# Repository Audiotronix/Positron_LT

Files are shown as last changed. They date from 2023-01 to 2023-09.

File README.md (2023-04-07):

<div align="center">

# Positron LT



**Navigation**

| [All Parts (BOM)](/Parts) | [Assembly](/Assembly) | [Software](/Software) | [Gallery](/Gallery) | [Download Repo](../../archive/refs/heads/main.zip)
| --- | --- | --- | --- | --- |

<br>

[](https://discord.gg/HJ44ZeGG2F)

</div>

<br>

## About

The Positron-LT is a printer made for everyone, especially hobbyists and professionals who don't want to or can't use machined parts.
This printer is a [RepRap](https://reprap.org/wiki/RepRap) version based on the innovative [Positron V3](https://github.com/KRALYN/PositronV3) formfactor and motion-system which was created by [KRALYN](https://github.com/KRALYN/PositronV3).

**Although the printer is printed, it can still be folded and thus still fits into a filament box. Thus, there are no disadvantages compared to the original, it may even have some improvements**

> Note: This project is a work in progress! The primary design is ready, updates and changes will be made continuously.

<br>

## LT
**LT** stands for **L**igh**T** 
Since the printer is made of printed parts instead of machined parts, it is lighter than the original Positron V3.

- Lighter to source
- Lighter to build
- Lighter to transport

<br>

## Advantages 

- No Machined Part
-	All mechanical parts can be sourced on websites like AliExpress, Amazon or your local hardware store.
- Much less parts to assemble than the V3
- Integrated PSU (power supply unit) with 200W
- 3mm GT2 timing belt on XY (cheaper and easier to source as the original Synchromesh wire)
- The base chassis is made of 10x10 [Makerbeam](https://www.makerbeam.com/makerbeam/) extrusions and other [Makerbeam](https://www.makerbeam.com/makerbeam/) parts. **All other structural parts can be printed!**
- Simplified Z axis by using a leadscrew. Easy to assemble by folding up
- Improved toolhead cooling
- could be used with larger XY Stepper motors up to 26mm

<br>

## Specs

-	Max Print Speed: 250mm/s (under investigation)
-	Max Travel Speed: 350mm/s (under investigation)
-	Acceleration: 9800mm/s^2 (under investigation)
-	Build Volume: 180x180x180mm
-	Weight: 2300-2500g (with integrated PSU)
-	Hotend max temp: 250C
-	Build Plate Max temp: 80-100C
-	Power supply: 24V; 200W
-	Footprint: ~200mmx200mm

<br>

# RepRap
RepRap means that most parts of the printer can be printed and nothing needs to be machined. Only basic tools like a drill or a saw are needed. All other parts are readily available and can be bought online or might even be available in a hardware store.

<br>

## License

Positron LT is a 3D printer design that is fully open source, which means anyone can use, modify, and share the design. We use a dual-licensing model to ensure that the project remains open source while providing a separate license for entities who want to use the design for financial gain.

### Licensing Explained

- **For personal, educational, and non-commercial use**: The design is available under the GNU General Public License v3.0 (GPLv3). This means you can use, modify, and share the design freely, as long as you also share any changes you make under the same dual-licensing model. This ensures that the open-source nature of the project is maintained. See the [GNU General Public License v3.0 (GPLv3)](LICENSE) file for the full text of the GPLv3.

- **For commercial use or financial gain**: We offer a custom commercial license for companies or individuals who want to use the design for commercial purposes or financial gain. This separate license includes a small royalty fee, which helps support the project. See the [Commercial License](LICENCE-COMMERCIAL) file for details.

### Contributing

We welcome and appreciate contributions to Positron LT! By contributing to this project, you agree that your contributions will be licensed under the dual-licensing model, with the GPLv3 applying to non-commercial use and contributions, and the commercial license applying for commercial use or financial gain.

### License Summary

Positron LT uses a dual-licensing model:

- The GNU General Public License v3.0 (GPLv3) for personal, educational, and non-commercial use and contributions. See the [GNU General Public License v3.0 (GPLv3)](LICENSE) file.
- A commercial license for commercial use or financial gain. See the [Commercial License](LICENCE-COMMERCIAL) file.

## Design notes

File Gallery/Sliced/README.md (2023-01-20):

# This page is still a work in progress! [<sub>(back)</sub>](../../../)
- You will soon find pictures and videos of the printer here

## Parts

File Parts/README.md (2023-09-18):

# The parts that make the Positron LT so great (BOM) [<sub>(back)</sub>](../../../)

| [BOM as .CSV](./bom.csv) | [Required Tools](../Assembly/#required-tools) | [Recommended Filaments](./Printed%20Parts#recommended-filaments) | [Download Printed Parts](https://minhaskamal.github.io/DownGit/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) |
| --- | --- | --- | --- |

>Note: None of these parts need to be machined! Everything can be bought, some parts might need to be shortened with a saw, and some holes need to be drilled, so only basic tools are required.

> There are various display types available. Please make sure you are using the right one

> We currently can not guarantee that all parts fit / work as expected

:exclamation: **These parts are not complete. Printhead and Extruder assemblies may be missing or are currently being developed.** :exclamation:

| You can also install [this extension](https://share-a-cart.com/) and fill your AliExpress cart with just one click.<br>Be aware that this shared cart includes every part besides the makerbeam parts.<br>Things like a raspberry or the psu are also included and might be cheaper when sourced elsewhere.<br><br>Cart id: [I1YPG](https://share-a-cart.com/get/I1YPG)<br><br> We don't know what happens when a store changes it's goods and the shared cart tries to add the product. So please check after importing the cart for completeness.|
| :--- |

</diV>

## [Printed Parts](./Printed%20Parts)

|                   Part Name                   | STL | STEP |Amount| Print Time | Used filament (g)|
| --- | --- | --- | --- | --- | --- |
| BASECOVER_LEFT_V01 | [STL](./Printed%20Parts/STL/BASECOVER_LEFT_V01.stl) | [STEP](./Printed%20Parts/STEP/BASECOVER_LEFT_V01.step) | 1 |  5h27m  |  52  |
| BASECOVER_RIGHT_V01 | [STL](./Printed%20Parts/STL/BASECOVER_RIGHT_V01.stl) | [STEP](./Printed%20Parts/STEP/BASECOVER_RIGHT_V01.step) | 1 |  5h44m  |  54  |
| BASEPART_BACK_V01 | [STL](./Printed%20Parts/STL/BASEPART_BACK_V01.stl) | [STEP](./Printed%20Parts/STEP/BASEPART_BACK_V01.step) | 1 |  6h7m  |  60  |
| BASEPART_FRONT_V01 | [STL](./Printed%20Parts/STL/BASEPART_FRONT_V01.stl) | [STEP](./Printed%20Parts/STEP/BASEPART_FRONT_V01.step) | 1 |  4h38m  |  43  |
| BASEPART_LEFT_V01 | [STL](./Printed%20Parts/STL/BASEPART_LEFT_V01.stl) | [STEP](./Printed%20Parts/STEP/BASEPART_LEFT_V01.step) | 1 |  4h24m  |  38  |
| BASEPART_RIGHT_V01 | [STL](./Printed%20Parts/STL/BASEPART_RIGHT_V01.stl) | [STEP](./Printed%20Parts/STEP/BASEPART_RIGHT_V01.step) | 1 |  4h0m  |  35  |
| BEDHOLDER_CONNECTOR_V01 | [STL](./Printed%20Parts/STL/BEDHOLDER_CONNECTOR_V01.stl) | [STEP](./Printed%20Parts/STEP/BEDHOLDER_CONNECTOR_V01.step) | 1 |  1h33m  |  13  |
| BED_HOLDER_MAIN_V01 | [STL](./Printed%20Parts/STL/BED_HOLDER_MAIN_V01.stl) | [STEP](./Printed%20Parts/STEP/BED_HOLDER_MAIN_V01.step) | 1 |  6h7m  |  60  |
| BELT-TENSIONER_Z_V01 | [STL](./Printed%20Parts/STL/BELT-TENSIONER_Z_V01.stl) | [STEP](./Printed%20Parts/STEP/BELT-TENSIONER_Z_V01.step) | 1 |  15m  |  1  |
| BELT_CONNECTOR_V01_WIP | [STL](./Printed%20Parts/STL/BELT_CONNECTOR_V01_WIP.stl) | [STEP](./Printed%20Parts/STEP/BELT_CONNECTOR_V01_WIP.step) | 1 |  ---  |  ---  |
| BELT_TENSIONER_XY_V01 | [STL](./Printed%20Parts/STL/BELT_TENSIONER_XY_V01.stl) | [STEP](./Printed%20Parts/STEP/BELT_TENSIONER_XY_V01.step) | 1 |  44m  |  6  |
| BOTTOM_COVER_V01 | [STL](./Printed%20Parts/STL/BOTTOM_COVER_V01.stl) | [STEP](./Printed%20Parts/STEP/BOTTOM_COVER_V01.step) | 1 |  19m  |  1  |
| COVER_ROUND_V01 | [STL](./Printed%20Parts/STL/COVER_ROUND_V01.stl) | [STEP](./Printed%20Parts/STEP/COVER_ROUND_V01.step) | 2 |  4m  |  1  |
| DISTANCE_LEFT_V01 | [STL](./Printed%20Parts/STL/DISTANCE_LEFT_V01.stl) | [STEP](./Printed%20Parts/STEP/DISTANCE_LEFT_V01.step) | 1 |  1h44m  |  13  |
| DISTANCE_RIGHT_V01 | [STL](./Printed%20Parts/STL/DISTANCE_RIGHT_V01.stl) | [STEP](./Printed%20Parts/STEP/DISTANCE_RIGHT_V01.step) | 1 |  59m  |  8  |
| ENDCAP_BED-EXTRUSION_V01 | [STL](./Printed%20Parts/STL/ENDCAP_BED-EXTRUSION_V01.stl) | [STEP](./Printed%20Parts/STEP/ENDCAP_BED-EXTRUSION_V01.step) | 2 |  6m  |  1  |
| EXTRUDER_BASEPLATE_V01 | [STL](./Printed%20Parts/STL/EXTRUDER_BASEPLATE_V01.stl) | [STEP](./Printed%20Parts/STEP/EXTRUDER_BASEPLATE_V01.step) | 1 |  7m  |  1  |
| INTERCONNECT_V03_WIP | [STL](./Printed%20Parts/STL/INTERCONNECT_V03_WIP.stl) | [STEP](./Printed%20Parts/STEP/INTERCONNECT_V03_WIP.step) | 1 |  ---  |  ---  |
| LEADSCREW_NUT_MOUNT_V01 | [STL](./Printed%20Parts/STL/LEADSCREW_NUT_MOUNT_V01.stl) | [STEP](./Printed%20Parts/STEP/LEADSCREW_NUT_MOUNT_V01.step) | 1 |  1h2m  |  6  |
| LED_INDICATOR_MOUNT_V01 | [STL](./Printed%20Parts/STL/LED_INDICATOR_MOUNT_V01.stl) | [STEP](./Printed%20Parts/STEP/LED_INDICATOR_MOUNT_V01.step) | 1 |  16m  |  1  |
| MOTORBRACKET_LEFT_V01 | [STL](./Printed%20Parts/STL/MOTORBRACKET_LEFT_V01.stl) | [STEP](./Printed%20Parts/STEP/MOTORBRACKET_LEFT_V01.step) | 1 |  3h17m  |  32  |
| MOTORBRACKET_RIGHT_V01 | [STL](./Printed%20Parts/STL/MOTORBRACKET_RIGHT_V01.stl) | [STEP](./Printed%20Parts/STEP/MOTORBRACKET_RIGHT_V01.step) | 1 |  3h16m  |  32  |
| PICO_MOUNT_PRE-SKETCH_V01 | [STL](./Printed%20Parts/STL/PICO_MOUNT_PRE-SKETCH_V01.stl) | [STEP](./Printed%20Parts/STEP/PICO_MOUNT_PRE-SKETCH_V01.step) | 1 |  20m  |  2  |
| SCREEN_BASE_V01_WIP | [STL](./Printed%20Parts/STL/SCREEN_BASE_V01_WIP.stl) | [STEP](./Printed%20Parts/STEP/SCREEN_BASE_V01_WIP.step) | 1 |  1h57m  |  20  |
| SCREEN_LID_V01_WIP | [STL](./Printed%20Parts/STL/SCREEN_LID_V01_WIP.stl) | [STEP](./Printed%20Parts/STEP/SCREEN_LID_V01_WIP.step) | 1 |  1h6m  |  9  |
| SCREWMOUNT_BOTTOM_V01 | [STL](./Printed%20Parts/STL/SCREWMOUNT_BOTTOM_V01.stl) | [STEP](./Printed%20Parts/STEP/SCREWMOUNT_BOTTOM_V01.step) | 1 |  59m  |  7  |
| SIDE_PANEL_LEFT_V01 | [STL](./Printed%20Parts/STL/SIDE_PANEL_LEFT_V01.stl) | [STEP](./Printed%20Parts/STEP/SIDE_PANEL_LEFT_V01.step) | 1 |  44m  |  5  |
| SIDE_PANEL_RIGHT_V01 | [STL](./Printed%20Parts/STL/SIDE_PANEL_RIGHT_V01.stl) | [STEP](./Printed%20Parts/STEP/SIDE_PANEL_RIGHT_V01.step) | 1 |  44m  |  5  |
| X-RAIL_ENDCAP_V01 | [STL](./Printed%20Parts/STL/X-RAIL_ENDCAP_V01.stl) | [STEP](./Printed%20Parts/STEP/X-RAIL_ENDCAP_V01.step) | 2 |  6m  |  1  |
| XY-SPACER_V01 | [STL](./Printed%20Parts/STL/XY-SPACER_V01.stl) | [STEP](./Printed%20Parts/STEP/XY-SPACER_V01.step) | 1 |  21m  |  3  |
| Z-AXIS-ENDSTOP_V01 | [STL](./Printed%20Parts/STL/Z-AXIS-ENDSTOP_V01.stl) | [STEP](./Printed%20Parts/STEP/Z-AXIS-ENDSTOP_V01.step) | 1 |  1h2m  |  8  |
| Z-BLOCK_HOLDER_V01 | [STL](./Printed%20Parts/STL/Z-BLOCK_HOLDER_V01.stl) | [STEP](./Printed%20Parts/STEP/Z-BLOCK_HOLDER_V01.step) | 1 |  42m  |  5  |

``Click on the links to be redirected to the file``<br>
``Print time and part weight are a result of slicing the parts in PrusaSlicer with .20 layer height (quality) for the PrusaMini``

<br>

## [Mechanical Parts](./Mechanical%20Parts)

### EXTRUDER:
|                    Part Name                    |CAD|                               Link                              |PCS | Price |                                                                                                                                 Note                                                                                                                                 |
| --- | --- | :---: | :---: | :---: | :--- |
| [ANGLED_EXTRUDER_MOD](./Mechanical%20Parts/ANGLED_EXTRUDER_MOD.stl) | 1 | [link](https://github.com/FramingApp/PositronV3B-High-Speed-Edition/blob/10x10makerbeams_w_screw_z_axis/CAD%20%20files/Angled%20Extruder%20Mod.stp) | --- | --- | Designed by HarryLoud: [link](https://github.com/FramingApp/PositronV3B-High-Speed-Edition/blob/10x10makerbeams_w_screw_z_axis/CAD%20%20files/Angled%20Extruder%20Mod.stp) |
| [CAPRICORN_PTFE_TUBE_1](./Mechanical%20Parts/CAPRICORN_PTFE_TUBE_1.stl) | 1 | [link](https://aliexpress.com/item/1005003433217588.html) / [link](https://amzn.to/3jBuaMN) | 1 | 8,25€ | About 60cm required |
| [HOTEND_COMPLETE](./Mechanical%20Parts/HOTEND_COMPLETE.stl) | 1 | [link](https://aliexpress.com/item/1005004802238357.html) | 1 | 35,77€ | Funssor hotend complete / will be replaced with Phaetus hotend when available  |

### ELECTRONICS:
|                    Part Name                    |CAD|                               Link                              |PCS | Price |                                                                                                                                 Note                                                                                                                                 |
| --- | --- | :---: | :---: | :---: | :--- |
| [10PIN_EXP_FEMALE](./Mechanical%20Parts/10PIN_EXP_FEMALE.stl) | 1 | [link](https://aliexpress.com/item/1005002431897617.html) | 10 | 0,88€ | Select 10P |
| [10PIN_MALE_CONNECTOR](./Mechanical%20Parts/10PIN_MALE_CONNECTOR.stl) | 1 | [link](https://aliexpress.com/item/33029492417.html) / [link](https://amzn.to/3XzUQMl) | 1 | 1,12€ | Select 2x5 10pin |
| [6_PIN_MAGNETIC_POGO](./Mechanical%20Parts/6_PIN_MAGNETIC_POGO.stl) | 1 | [link](https://aliexpress.com/item/1005002669709542.html) | 1 | 3,30€ | Select 6pin Straight |
| [C7_PLUG-IN](./Mechanical%20Parts/C7_PLUG-IN.stl) | 1 | [link](https://aliexpress.com/item/4001252791878.html) | 1 | 0,23€ |  |
| [CABLE_C7_SWITCH](./Mechanical%20Parts/CABLE_C7_SWITCH.stl) | 1 | [link](https://amzn.to/3w4nDgk) / [link](https://amzn.to/3XzU6qx) | 1 | 9,99€ | We recommend using a cable with a switch or an adapter like this: [link](https://aliexpress.com/item/1005002301827800.html) / [link](https://amzn.to/3XzSGfH) |
| [EPP-200-24](./Mechanical%20Parts/EPP-200-24.stl) | 1 | [link](https://www.mouser.de/ProductDetail/MEAN-WELL/EPP-200-24?qs=C9r8PV%2F%252BoWOh4U0pNOxnkQ%3D%3D) / [link](https://amzn.to/3WfsBS9) | 1 | 52,30€ | Meanwell EPP-200-24 !! Note from Muon3D: If theMuon3D heated bed is being used, the EPP-200-27 improves its performance by 30-40%. (70-80w at 24v, 90-100w at 27v). [link](https://www.mouser.de/ProductDetail/MEAN-WELL/EPP-200-27?qs=C9r8PV%2F%252BoWPXQf6mJFm6HA%3D%3D) |
| [FAN_2510](./Mechanical%20Parts/FAN_2510.stl) | 2 | [link](https://aliexpress.com/item/32807610078.html) / [link](https://amzn.to/3iCEaVR) | 2 | 10,69€ | 24V Dual Ball XH2,54 |
| [FAN_3010](./Mechanical%20Parts/FAN_3010.stl) | 1 | [link](https://aliexpress.com/item/1005002568592831.html?) | 1 | 3,59€ | Select 24V xh2.54 2pin |
| [FAN_5015](./Mechanical%20Parts/FAN_5015.stl) | 1 | [link](https://aliexpress.com/item/1005002517858129.html) / [link](https://aliexpress.com/item/32844339310.html) | 1 | 8,67€ | Select 24V model |
| [HEATED_GLASSBED_MUON-3D](./Mechanical%20Parts/HEATED_GLASSBED_MUON-3D.stl) | 1 | [link](https://muon3d.com/products/positron-v3-transparent-heated-bed) | 1 | 45,95€ | Highly recomended !! Note from Muon3D: If theMuon3D heated bed is being used, the EPP-200-27 improves its performance by 30-40%. (70-80w at 24v, 90-100w at 27v). [link](https://www.mouser.de/ProductDetail/MEAN-WELL/EPP-200-27?qs=C9r8PV%2F%252BoWPXQf6mJFm6HA%3D%3D) |
| [HEATER_CARTRIGE_1](./Mechanical%20Parts/HEATER_CARTRIGE_1.stl) | 1 | [link](https://aliexpress.com/item/32843289523.html) | 1 | 1,27€ | Select 24V 50W 1M |
| [HEAT_SINK_RPI_2MM](./Mechanical%20Parts/HEAT_SINK_RPI_2MM.stl) | 1 | [link](https://aliexpress.com/item/1005004772727034.html) | 1 | 5,72€ | 2mm height |
| [LED_4X_15X15](./Mechanical%20Parts/LED_4X_15X15.stl) | 1 | [link](https://aliexpress.com/item/1005002674028098.html) | 1 | 0,45€ | Select 4Bit Rectangular |
| [MINI_IR_SENSOR](./Mechanical%20Parts/MINI_IR_SENSOR.stl) | 1 | [link](https://aliexpress.com/item/32995184975.html) | 1 | 18,20€ |  |
| [MOTOR_17HS08-1004S](./Mechanical%20Parts/MOTOR_17HS08-1004S.stl) | 3 | [link](https://www.omc-stepperonline.com/de/nema-17-bipolar-0-9deg-11ncm-15-6oz-in-1-2a-3-6v-42x42x21mm-4-draehte-17hm08-1204s) / [link](https://amzn.to/3iEKg85) | 1 | 8,28€ |  |
| [RPI_ZERO_2W](./Mechanical%20Parts/RPI_ZERO_2W.stl) | 1 | [link](https://www.reichelt.de/raspberry-pi-zero-2-w-4x-1-ghz-512-mb-ram-wlan-bt-rasp-pi-zero2-w-p313902.html) / [link](https://amzn.to/3IR9ASM) | 1 | 22,50€ | You can also use an Bananapi Pi M2 Zero as substituion: [link](https://github.com/FramingApp/BananaPi_Positron_Klipper_Moonraker_Fluidd) |
| [SKR-PICO](./Mechanical%20Parts/SKR-PICO.stl) | 1 | [link](https://biqu.equipment/en-au/products/btt-skr-pico-v1-0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) / [link](https://amzn.to/3QKw7Tj) | 1 | 29,99€ |  |
| [TFT_35](./Mechanical%20Parts/TFT_35.stl) | 1 | [link](https://aliexpress.com/item/1005004864671870.html) / [link](https://amzn.to/3l8vAPt) | 1 | 17,34€ |  |
| [THERMISTOR_1](./Mechanical%20Parts/THERMISTOR_1.stl) | 1 | [link](aliexpress.com/item/32812361274.html) / [link](https://amzn.to/3Y2qRxg) | 5 | 2,17€ | Select with XH2.54 terminal |

### FASTENERS:
|                    Part Name                    |CAD|                               Link                              |PCS | Price |                                                                                                                                 Note                                                                                                                                 |
| --- | --- | :---: | :---: | :---: | :--- |
| [DIN_7979_M3X4X12](./Mechanical%20Parts/DIN_7979_M3X4X12.stl) | 2 | [link](https://aliexpress.com/item/1005003200850626.html) | 5 | 4,30€ | Select M3 (OD 4mm), 12mm (5pcs) |
| [DIN_7991_M3X12](./Mechanical%20Parts/DIN_7991_M3X12.stl) | 4 | [link](https://aliexpress.com/item/1005003107985358.html) / [link](https://amzn.to/3lbRscQ) | 50 | 2,06€ |  |
| [DIN_7991_M3X14](./Mechanical%20Parts/DIN_7991_M3X14.stl) | 41 | [link](https://aliexpress.com/item/1005003107985358.html) / [link](https://amzn.to/3JEOpDX) | 50 | 2,28€ |  |
| [DIN_7991_M3X16](./Mechanical%20Parts/DIN_7991_M3X16.stl) | 4 | [link](https://aliexpress.com/item/1005003107985358.html) / [link](https://amzn.to/3l1bwhH) | 50 | 2,04 |  |
| [DIN_7991_M3X18](./Mechanical%20Parts/DIN_7991_M3X18.stl) | 7 | [link](https://aliexpress.com/item/1005003107985358.html) | 50 | 2,99€ |  |
| [DIN_7991_M3X25](./Mechanical%20Parts/DIN_7991_M3X25.stl) | 5 | [link](https://aliexpress.com/item/1005003107985358.html) / [link](https://amzn.to/3WZ3N0Z) | 50 | 3,68€ |  |
| [DIN_7991_M3X35](./Mechanical%20Parts/DIN_7991_M3X35.stl) | 12 | [link](https://aliexpress.com/item/1005003107985358.html) | 50 | 4,72€ |  |
| [DIN_7991_M3X8](./Mechanical%20Parts/DIN_7991_M3X8.stl) | 8 | [link](https://aliexpress.com/item/1005003107985358.html) / [link](https://amzn.to/3wUBpmc) | 50 | 1,58€ |  |
| [DIN_912_M3X20](./Mechanical%20Parts/DIN_912_M3X20.stl) | 5 | [link](https://aliexpress.com/item/1005003106092326.html) | 10 | 1,48€ |  |
| [DIN_912_M3X6](./Mechanical%20Parts/DIN_912_M3X6.stl) | 10 | [link](https://aliexpress.com/item/1005003106092326.html) | 10 | 0,78€ |  |
| [DIN_934_M3](./Mechanical%20Parts/DIN_934_M3.stl) | 2 | [link](https://aliexpress.com/item/1005003106199633.html) | 50 | 1,36€ |  |
| [M3_INSERT](./Mechanical%20Parts/M3_INSERT.stl) | 22 | [link](https://aliexpress.com/item/1005004879644825.html) / [link](https://amzn.to/3CRKrUf) | 50 | 0,35€ | Select M3(OD4.5mm), Length 5mm 50pcs |
| [THUMBSCREW_M6X16](./Mechanical%20Parts/THUMBSCREW_M6X16.stl) | 1 | [link](https://aliexpress.com/item/1005004651298319.html) | 2 | 1,90€ | Select M6 2pcs, 16mm |
| [WAFERHEAD_M3X10](./Mechanical%20Parts/WAFERHEAD_M3X10.stl) | 19 | [link](https://aliexpress.com/item/1005004510664424.html) | 20 | 1,97€ |  |
| [WAFERHEAD_M3X14](./Mechanical%20Parts/WAFERHEAD_M3X14.stl) | 4 | [link](https://aliexpress.com/item/1005004510664424.html) | 20 | 2,10€ |  |
| [WAFERHEAD_M3X20](./Mechanical%20Parts/WAFERHEAD_M3X20.stl) | 5 | [link](https://aliexpress.com/item/1005004510664424.html) | 20 | 2,54€ |  |

### MAKERBEAM:
Since Makerbeam does not sell beams with the needed length, they can either be cut by makerbeam or yourself. A cut by makerbeam costs 3.50€ you can find that service here:  [link](https://www.makerbeam.com/cut-and-tap-for-10x10mm.html) . Either way, you need to buy beams that are able to be cut in the desired lengths for which we created a cutting plan that can be found here: [link](https://github.com/Audiotronix/Positron_LT/blob/main/Parts/makerbeam_cuttingplan.pdf)
|                    Part Name                    |CAD|                               Link                              |PCS | Price |                                                                                                                                 Note                                                                                                                                 |
| --- | --- | :---: | :---: | :---: | :--- |
| [DIN_34805_M3X4](./Mechanical%20Parts/DIN_34805_M3X4.stl) | 7 |  | 25 | --- | Included with T-slot nut |
| [DIN_7991_M3X4](./Mechanical%20Parts/DIN_7991_M3X4.stl) | 3 |  | 25 | --- | Included with T-slot nut |
| [MAKERBEAM-CUBE](./Mechanical%20Parts/MAKERBEAM-CUBE.stl) | 3 | [link](https://www.makerbeam.com/makerbeam-corner-cubes-12p-black-for-makerbeam.html?id=24117589) / [link](https://amzn.eu/2M0ya10) | 12 | 17,95€ | You can buy single cubes here: [link](https://amzn.eu/2M0ya10) |
| [MAKERBEAM-CUBE_M6](./Mechanical%20Parts/MAKERBEAM-CUBE_M6.stl) | 1 |  | --- | --- | Included in previous cube order if ordered from makerbeam, otherwise can be ordered here: [link](https://amzn.eu/2M0ya10) |
| [MAKERBEAM_L-BRACKET_100304](./Mechanical%20Parts/MAKERBEAM_L-BRACKET_100304.stl) | 7 | [link](https://www.makerbeam.com/makerbeam-90-degree-brackets-12p.html?id=24117637) | 12 | 6,95€ |  |
| [MAKERBEAM_L165](./Mechanical%20Parts/MAKERBEAM_L165.stl) | 2 | [link](https://www.makerbeam.com/makerbeam/makerbeam-10x10mm-profile-lengths-anodised-in-blac/) | --- | -> | You can find more infos about the beams in the text below the category name [link](https://github.com/Audiotronix/Positron_LT/tree/main/Parts#makerbeam) |
| [MAKERBEAM_L200](./Mechanical%20Parts/MAKERBEAM_L200.stl) | 2 | [link](https://www.makerbeam.com/makerbeam/makerbeam-10x10mm-profile-lengths-anodised-in-blac/) | --- | -> | You can find more infos about the beams in the text below the category name [link](https://github.com/Audiotronix/Positron_LT/tree/main/Parts#makerbeam) |
| [MAKERBEAM_L230](./Mechanical%20Parts/MAKERBEAM_L230.stl) | 1 | [link](https://www.makerbeam.com/makerbeam/makerbeam-10x10mm-profile-lengths-anodised-in-blac/) | --- | -> | You can find more infos about the beams in the text below the category name [link](https://github.com/Audiotronix/Positron_LT/tree/main/Parts#makerbeam) |
| [MAKERBEAM_L240](./Mechanical%20Parts/MAKERBEAM_L240.stl) | 2 | [link](https://www.makerbeam.com/makerbeam/makerbeam-10x10mm-profile-lengths-anodised-in-blac/) | --- | -> | You can find more infos about the beams in the text below the category name [link](https://github.com/Audiotronix/Positron_LT/tree/main/Parts#makerbeam) |
| [MAKERBEAM_L250](./Mechanical%20Parts/MAKERBEAM_L250.stl) | 3 | [link](https://www.makerbeam.com/makerbeam/makerbeam-10x10mm-profile-lengths-anodised-in-blac/) | --- | -> | You can find more infos about the beams in the text below the category name [link](https://github.com/Audiotronix/Positron_LT/tree/main/Parts#makerbeam) |
| [MAKERBEAM_L30](./Mechanical%20Parts/MAKERBEAM_L30.stl) | 1 | [link](https://www.makerbeam.com/makerbeam/makerbeam-10x10mm-profile-lengths-anodised-in-blac/) | --- | -> | You can find more infos about the beams in the text below the category name [link](https://github.com/Audiotronix/Positron_LT/tree/main/Parts#makerbeam) |
| [MAKERBEAM_T-NUT_101619-1](./Mechanical%20Parts/MAKERBEAM_T-NUT_101619-1.stl) | 33 | [link](https://www.makerbeam.com/makerbeam-t-slot-nuts-for-makerbeam-25p.html) / [link](https://amzn.to/3DGxXPI) | 25 | 14,98€ | Order the big pack: [link](https://www.makerbeam.com/makerbeam-t-slot-nuts-for-makerbeam-25p.html) and a small one: [link](https://www.makerbeam.com/linear-slide-kit-t-slot-nuts-5p-and-5mm-bolts-m3-1.html) / [link](https://amzn.to/3DGxXPI) |

### MOTION:
|                    Part Name                    |CAD|                               Link                              |PCS | Price |                                                                                                                                 Note                                                                                                                                 |
| --- | --- | :---: | :---: | :---: | :--- |
| [F5-10_BEARING](./Mechanical%20Parts/F5-10_BEARING.stl) | 2 | [link](https://aliexpress.com/item/4000211452548.html) / [link](https://amzn.to/3l24CZH) | 1 | 0,27€ |  |
| [F683_OPEN_BEARING-H25-](./Mechanical%20Parts/F683_OPEN_BEARING-H25-.stl) | 28 | [link](aliexpress.com/item/1005004282333265.html) | 10 | 2,95€ | Select 3 times |
| [GT2_16T_IDLER_SMOOTH](./Mechanical%20Parts/GT2_16T_IDLER_SMOOTH.stl) | 1 | [link](https://aliexpress.com/item/32971394035.html) / [link](https://amzn.to/3DF3bad) | 1 | 0,55€ | Select 16T W6 B3 Without T |
| [GT2_BELT-3MM_L1650MM](./Mechanical%20Parts/GT2_BELT-3MM_L1650MM.stl) | 1 | [link](https://www.ebay.de/itm/283457733982?var=585183190920) / [link](https://amzn.to/3wUc9MT) | 1 | 5,00€ | Select x 2m (Y32) (You also can cut an 6mm belt in 2pieces. recommented cut at~2,8mm) |
| [GT2_BELT-6MM_L178MM](./Mechanical%20Parts/GT2_BELT-6MM_L178MM.stl) | 1 | [link](https://aliexpress.com/item/1005004100120790.html) / [link](https://amzn.to/3DIaihV) | 1 | 1,07€ | Select 2GT-178, Belt Width 6mm 1pcs |
| [LEADSCREW_NUT_T5X4](./Mechanical%20Parts/LEADSCREW_NUT_T5X4.stl) | 1 | [link](https://www.ebay.de/itm/165688561910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) | 1 | 1,49€ | Only needs to be bought if no screw is included with rod! Select T5x1x4 Brass/POM |
| [LEADSCREW_T5X4_L225](./Mechanical%20Parts/LEADSCREW_T5X4_L225.stl) | 1 | [link](https://aliexpress.com/item/1005004583759873.html) / [link](https://www.ebay.de/itm/165688561901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) | 1 | 10,15€ | Select 250mm, Pitch 1mm Lead 4mm / Second link has no screw! |
| [MF85_BEARING](./Mechanical%20Parts/MF85_BEARING.stl) | 2 | [link](https://aliexpress.com/item/1005004881583203.html) / [link](https://amzn.to/3HTb6mI) | 1 | 0,72€ | Select MF85ZZ 5X8X2.5mm |
| [MGN12-C_CARRIAGE](./Mechanical%20Parts/MGN12-C_CARRIAGE.stl) | 1 |  | 1 | --- | Mostly includet with the rails |
| [MGN12_RAIL_L225](./Mechanical%20Parts/MGN12_RAIL_L225.stl) | 1 | [link](https://amzn.to/3H8WS0A) | 1 | 18,99€ | 250mm MGN12C |
| [MGN9-C_CARRIAGE](./Mechanical%20Parts/MGN9-C_CARRIAGE.stl) | 1 |  | 1 | --- | Mostly includet with the rails |
| [MGN9_RAIL_L227](./Mechanical%20Parts/MGN9_RAIL_L227.stl) | 1 | [link](https://amzn.to/3Wfy7UH) | 1 | 20,99€ | 250mm MGN9C |
| [MGW9-C_CARRIAGE](./Mechanical%20Parts/MGW9-C_CARRIAGE.stl) | 1 |  | 1 | --- | Mostly includet with the rails |
| [MGW9_RAIL_L227](./Mechanical%20Parts/MGW9_RAIL_L227.stl) | 1 | [link](https://www.ebay.de/itm/234306987115?var=533899872753) / [link](https://amzn.to/3Xxt5Uz) | 1 | 19,40€ | 250mm MGW9C |
| [MR115_BEARING](./Mechanical%20Parts/MR115_BEARING.stl) | 1 | [link](https://aliexpress.com/item/32995122493.html) / [link](https://amzn.to/3HvHSsA) | 10 | 0,94€ |  |
| [MR117_2Z_BEARING](./Mechanical%20Parts/MR117_2Z_BEARING.stl) | 10 | [link](https://aliexpress.com/item/4000891798197.html) / [link](https://amzn.to/3RulK6u) | 5 | 2,71€ | Select MR117ZZ 7x11x3mm |
| [PULLEY_T20_LOWPROFILE](./Mechanical%20Parts/PULLEY_T20_LOWPROFILE.stl) | 4 | [link](https://aliexpress.com/item/32913757229.html) | 1 | 0,99€ | Select 20T Bore 5mm |

### SHIMS:
|                    Part Name                    |CAD|                               Link                              |PCS | Price |                                                                                                                                 Note                                                                                                                                 |
| --- | --- | :---: | :---: | :---: | :--- |
| [DIN_125_M5](./Mechanical%20Parts/DIN_125_M5.stl) | 2 | [link](https://aliexpress.com/item/1005002148389665.html) | 25 | 1,48€ | Select M5(25PCS) |
| [DIN_433_M3](./Mechanical%20Parts/DIN_433_M3.stl) | 12 | [link](https://aliexpress.com/item/4001213983709.html) | 100 | 2,21€ | Select 3x6x0.5 |
| [DIN_988_7X13X02](./Mechanical%20Parts/DIN_988_7X13X02.stl) | 40 | [link](https://aliexpress.com/item/1005002046188859.html) / [link](https://amzn.to/3DF8rdF) | 50 | 1,91€ | Select 50pcs M7x13xThick, Thick 0.2mm |
| [DIN_988_M3X02](./Mechanical%20Parts/DIN_988_M3X02.stl) | 8 | [link](https://aliexpress.com/item/1005001878233881.html) / [link](https://amzn.to/3X3Y1LN) | 50 | 1,26€ | Select M3x6xThick 50pcs, 0.2mm thick |

|                    Part Name                    |CAD|                               Link                              |PCS | Price |                                                                                                                                 Note                                                                                                                                 |
| --- | --- | :---: | :---: | :---: | :--- |
| [BUFFER_BOTTOM](./Mechanical%20Parts/BUFFER_BOTTOM.stl) | 4 | [link](https://aliexpress.com/item/1005001559607723.html) | 100 | 1,06€ |  |
| [DUST_COVER_85X52](./Mechanical%20Parts/DUST_COVER_85X52.stl) | 2 | [link](https://aliexpress.com/item/4001283014835.html) | --- | --- | Highly recommended!  need to be cutted in 85x52mm and clued under the air shrout left and right |
| [PCB_SCREEN_ADAPTER](./Mechanical%20Parts/PCB_SCREEN_ADAPTER.stl) | 1 |  | --- | --- | Custom PCB, WIP |
| [SILICONE_SOCK_1](./Mechanical%20Parts/SILICONE_SOCK_1.stl) | 1 |  | --- | --- | Needs to be molded by yourself (WIP) |
| [SPACER_PRINTBED_WIP](./Mechanical%20Parts/SPACER_PRINTBED_WIP.stl) | 2 |  | --- | --- | Bed-End-Spacer WIP |

``Click on the part name to see a 3D model of it (mechanical parts are not intedet to be printed!)``<br>
``Price is based on the first/main link of each product``

> Note: Some links might be affiliate links!

## Total
| Category | Total | Exact Price |
| --- | --- | --- |
| EXTRUDER | 44,02€ | 44,02€ |
| ELECTRONICS | 259,2€ | 256,67€ |
| FASTENERS | 36,13€ | 11,67€ |
| MAKERBEAM | 54,86€<br>+29,35€ | 28,31€<br>+29,35€ |
| MOTION | 98,79€ | 97,35€ |
| SHIMS | 6,86€ | 2,12€ |
| OTHER | 1,06€ | 0,04€ |
| | | |
| Total | 530,27€ | 469,53€ |

> Note: Prices were calculated 20.01.2023, so might no longer be accurate

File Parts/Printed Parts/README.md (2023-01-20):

# Printing the Positron LT parts
| [Download 3D Files](https://minhaskamal.github.io/DownGit/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) |
| --- |

>Note: These are suggestions, I designed the LT with these in mind but other settings might work aswell. The Design is based on an 0.4mm Nozzle

## Recommended Filaments:

>Note: We absolutely recommend using a technical material without any flexibility that can withstand high temperatures. Tested Filaments:

| Type | Brand | Name | Price | Link | Required Nozzle |
| --- | --- | --- | --- | --- | --- |
| PC Blend | Prusament | Carbon Fiber | 59.99€ | [link](https://www.prusa3d.com/product/prusament-pc-blend-carbon-fiber-black-800g-2/) | Hardened |
| GreenTEC | extrudr | Pro Carbon | 49.99€ | [link](https://amzn.to/3ZJIYcK) | Hardened |
| ASA | Prusament | Prusament ASA | 29.99€ | [link](https://www.prusa3d.com/category/prusament-asa/) | --- |

> Note: Some links might be affiliate links!

## Slicing:

| Layer height | Infill | Supports | Perimeters | Horizontal shells | 
| --- | --- | --- | --- | --- |
| 0.2mm | 40% | On build plate only | 5 (min) | Top: 9, Bot: 8 |

## Printing:
| Part Name | Orientation | Supports | Prepared |
| :---: | --- | --- | --- |
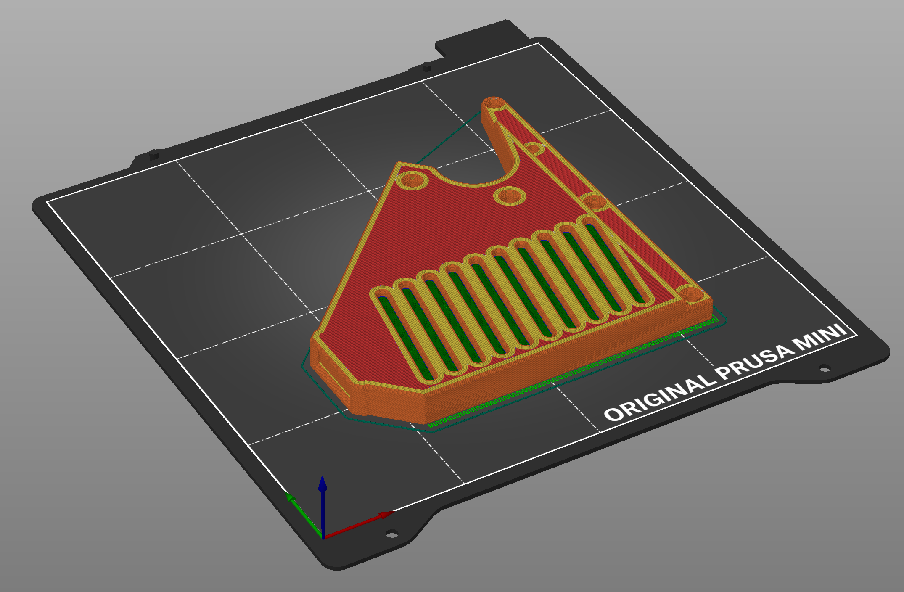
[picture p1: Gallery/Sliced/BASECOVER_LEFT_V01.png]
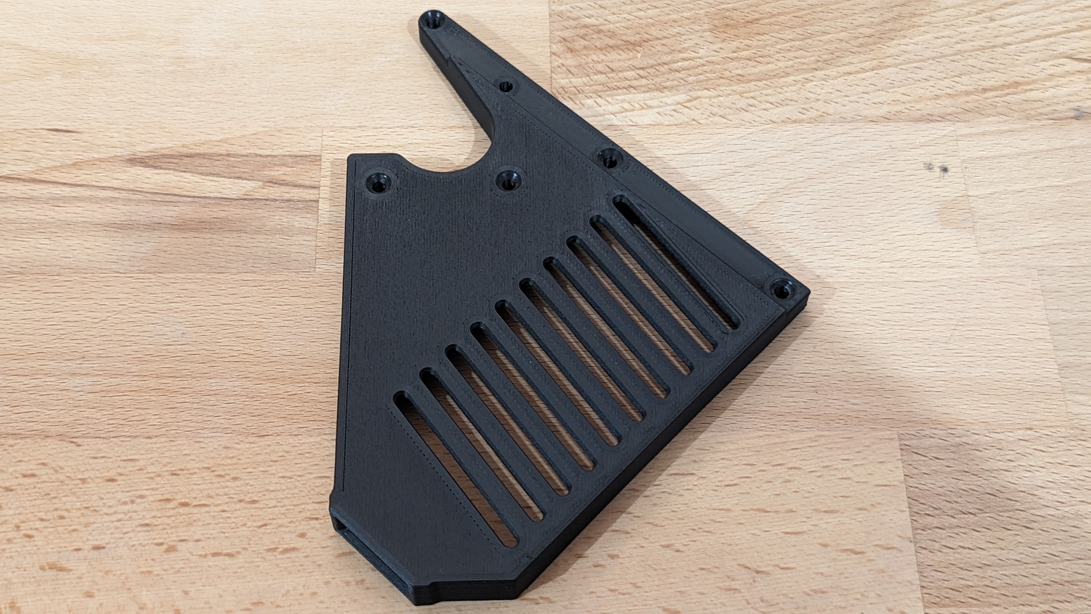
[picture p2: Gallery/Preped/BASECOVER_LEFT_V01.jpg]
|[BASECOVER_LEFT_V01](./STL/BASECOVER_LEFT_V01.stl) |  |  Supports on build plate only  | |
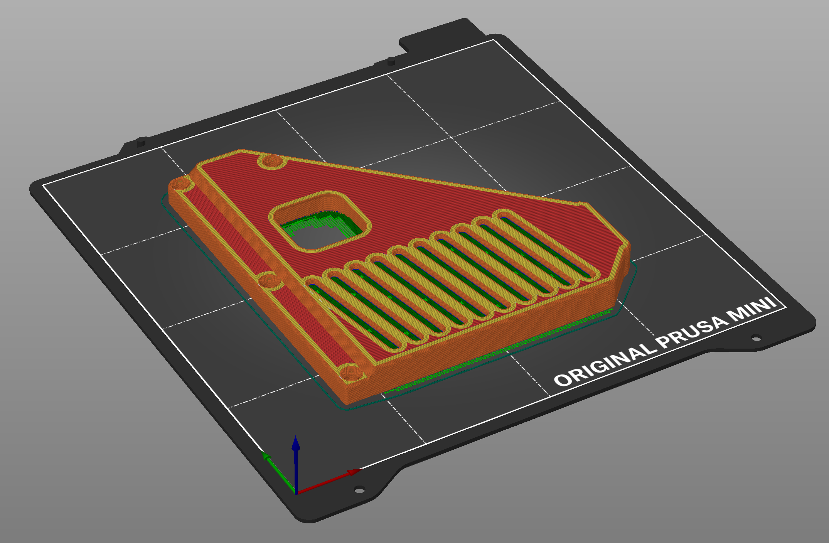
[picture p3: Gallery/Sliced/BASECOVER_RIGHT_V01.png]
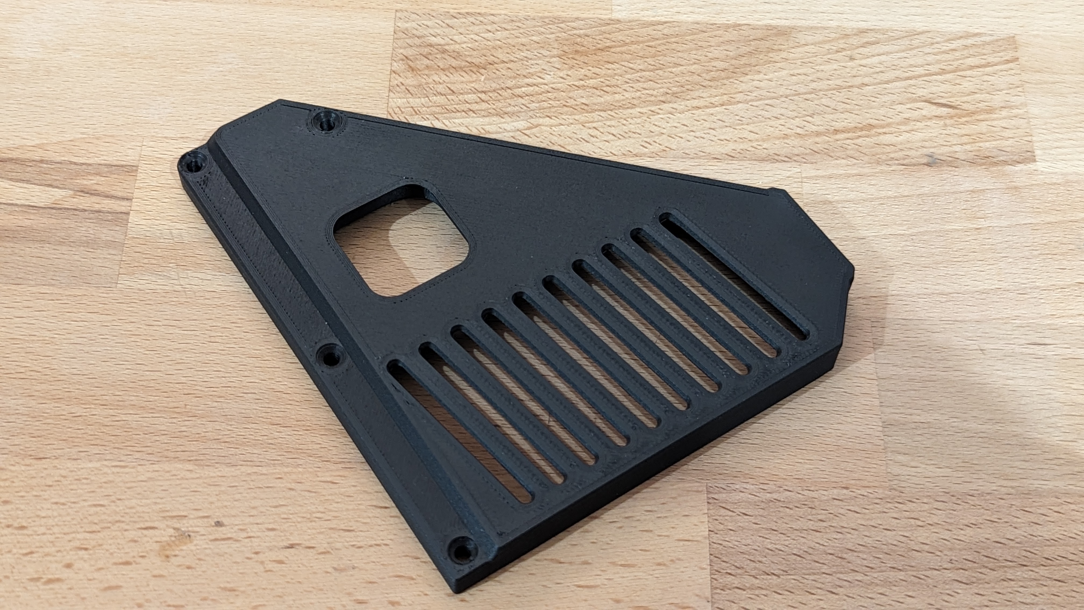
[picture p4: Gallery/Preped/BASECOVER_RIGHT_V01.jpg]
|[BASECOVER_RIGHT_V01](./STL/BASECOVER_RIGHT_V01.stl) |  |  Supports on build plate only  | |
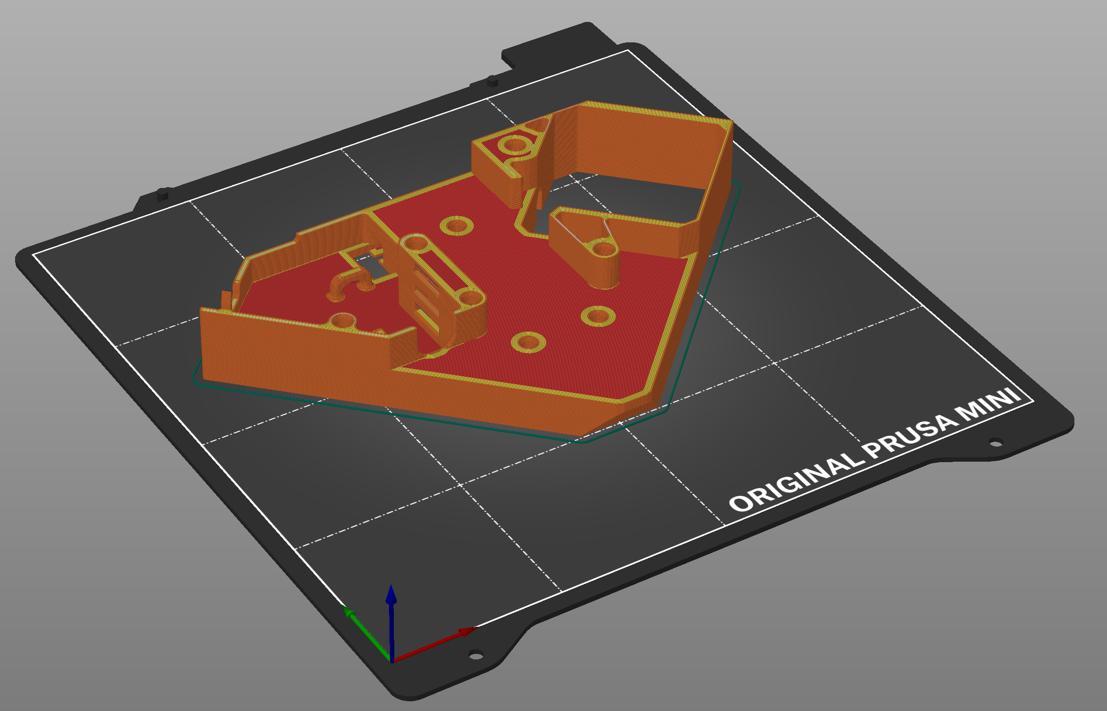
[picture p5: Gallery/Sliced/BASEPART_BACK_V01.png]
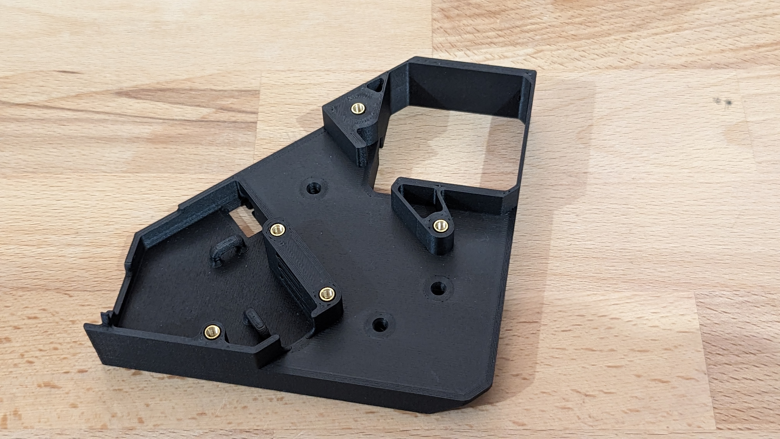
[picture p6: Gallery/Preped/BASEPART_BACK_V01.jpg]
|[BASEPART_BACK_V01](./STL/BASEPART_BACK_V01.stl) |  |  No supports needed  | |
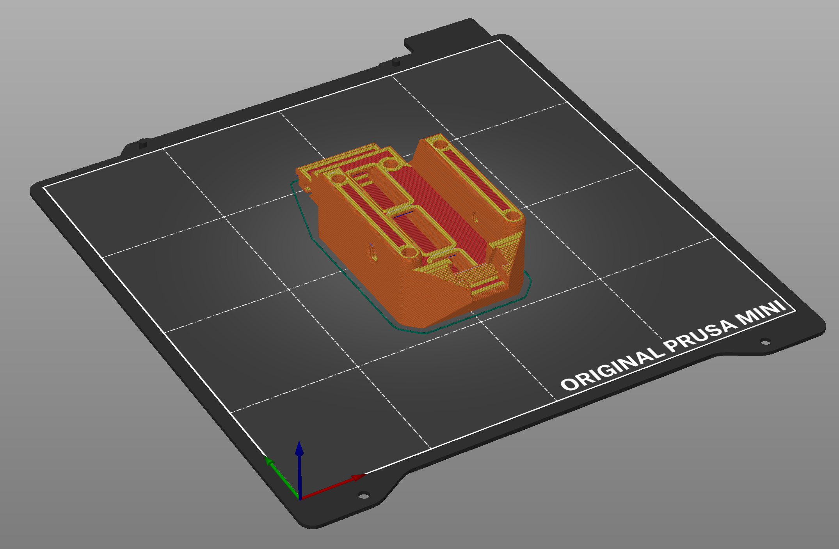
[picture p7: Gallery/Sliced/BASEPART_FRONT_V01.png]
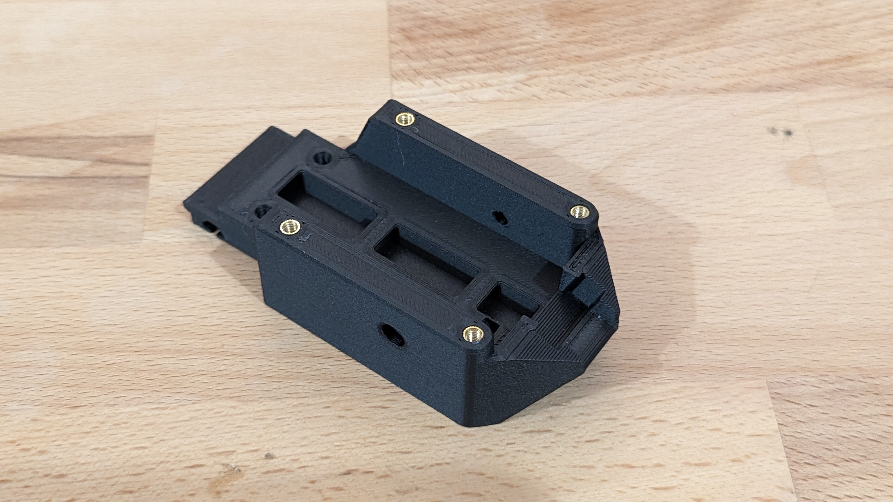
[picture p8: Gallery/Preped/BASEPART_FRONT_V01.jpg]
|[BASEPART_FRONT_V01](./STL/BASEPART_FRONT_V01.stl) |  |  No supports needed  | |
|[BASEPART_LEFT_V01](./STL/BASEPART_LEFT_V01.stl) |  |  Supports on build plate only  | |
|[BASEPART_RIGHT_V01](./STL/BASEPART_RIGHT_V01.stl) |  |  Supports on build plate only  | |
|[BEDHOLDER_CONNECTOR_V01](./STL/BEDHOLDER_CONNECTOR_V01.stl) |  |  No supports needed  | |
|[BED_HOLDER_MAIN_V01](./STL/BED_HOLDER_MAIN_V01.stl) |  |  Supports on build plate only  | |
|[BELT-TENSIONER_Z_V01](./STL/BELT-TENSIONER_Z_V01.stl) |  |  No supports needed  | |
|[BELT_CONNECTOR_V01_WIP](./STL/BELT_CONNECTOR_V01_WIP.stl) |  |  ---  | |
|[BELT_TENSIONER_XY_V01](./STL/BELT_TENSIONER_XY_V01.stl) |  |  No supports needed  | |
|[BOTTOM_COVER_V01](./STL/BOTTOM_COVER_V01.stl) |  |  ---  | |
|[COVER_ROUND_V01](./STL/COVER_ROUND_V01.stl) |  |  No supports needed  | |
|[DISTANCE_LEFT_V01](./STL/DISTANCE_LEFT_V01.stl) |  |  No supports needed  | |
|[DISTANCE_RIGHT_V01](./STL/DISTANCE_RIGHT_V01.stl) |  |  No supports needed  | |
|[ENDCAP_BED-EXTRUSION_V01](./STL/ENDCAP_BED-EXTRUSION_V01.stl) |  |  No supports needed  | |
|[EXTRUDER_BASEPLATE_V01](./STL/EXTRUDER_BASEPLATE_V01.stl) |  |  ---  | |
|[INTERCONNECT_V03_WIP](./STL/INTERCONNECT_V03_WIP.stl) |  |  ---  | |
|[LEADSCREW_NUT_MOUNT_V01](./STL/LEADSCREW_NUT_MOUNT_V01.stl) |  |  No supports needed  | |
|[LED_INDICATOR_MOUNT_V01](./STL/LED_INDICATOR_MOUNT_V01.stl) |  |  No supports needed  | |
|[MOTORBRACKET_LEFT_V01](./STL/MOTORBRACKET_LEFT_V01.stl) |  |  No supports needed  | |
|[MOTORBRACKET_RIGHT_V01](./STL/MOTORBRACKET_RIGHT_V01.stl) |  |  No supports needed  | |
|[PICO_MOUNT_PRE-SKETCH_V01](./STL/PICO_MOUNT_PRE-SKETCH_V01.stl) |  |  No supports needed  | |
|[SCREEN_BASE_V01_WIP](./STL/SCREEN_BASE_V01_WIP.stl) |  |  Supports on build plate only  | |
|[SCREEN_LID_V01_WIP](./STL/SCREEN_LID_V01_WIP.stl) |  |  No supports needed  | |
|[SCREWMOUNT_BOTTOM_V01](./STL/SCREWMOUNT_BOTTOM_V01.stl) |  |  Supports on build plate only  | |
|[SIDE_PANEL_LEFT_V01](./STL/SIDE_PANEL_LEFT_V01.stl) |  |  No supports needed  | |
|[SIDE_PANEL_RIGHT_V01](./STL/SIDE_PANEL_RIGHT_V01.stl) |  |  No supports needed  | |
|[X-RAIL_ENDCAP_V01](./STL/X-RAIL_ENDCAP_V01.stl) |  |  No supports needed  | |
|[XY-SPACER_V01](./STL/XY-SPACER_V01.stl) |  |  No supports needed  | |
|[Z-AXIS-ENDSTOP_V01](./STL/Z-AXIS-ENDSTOP_V01.stl) |  |  Supports on build plate only  | |
|[Z-BLOCK_HOLDER_V01](./STL/Z-BLOCK_HOLDER_V01.stl) |  |  No supports needed  | |
<div name='table_end'/>

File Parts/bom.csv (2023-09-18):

type | category | cad_name | amount | price | pcs | link | alt_link | note
printed |  | BASECOVER_LEFT_V01 | 1 | --- | 1 | --- | --- | [t: 5h27m |w: 52 |s: Supports on build plate only |]
printed |  | BASECOVER_RIGHT_V01 | 1 | --- | 1 | --- | --- | [t: 5h44m |w: 54 |s: Supports on build plate only |]
printed |  | BASEPART_BACK_V01 | 1 | --- | --- | --- | --- | [t: 6h7m |w: 60 |s: No supports needed |]
printed |  | BASEPART_FRONT_V01 | 1 | --- | 1 | --- | --- | [t: 4h38m |w: 43 |s: No supports needed |]
printed |  | BASEPART_LEFT_V01 | 1 | --- | 1 | --- | --- | [t: 4h24m |w: 38 |s: Supports on build plate only |]
printed |  | BASEPART_RIGHT_V01 | 1 | --- | 1 | --- | --- | [t: 4h0m |w: 35 |s: Supports on build plate only |]
printed |  | BEDHOLDER_CONNECTOR_V01 | 1 | --- | 1 | --- | --- | [t: 1h33m |w: 13 |s: No supports needed |]
printed |  | BED_HOLDER_MAIN_V01 | 1 | --- | 1 | --- | --- | [t: 6h7m |w: 60 |s: Supports on build plate only |]
printed |  | BELT-TENSIONER_Z_V01 | 1 | --- | 1 | --- | --- | [t: 15m |w: 1 |s: No supports needed |]
printed |  | BELT_CONNECTOR_V01_WIP | 1 | --- | --- | --- | --- | [t: --- |w: --- |s: --- |]
printed |  | BELT_TENSIONER_XY_V01 | 1 | --- | --- | --- | --- | [t: 44m |w: 6 |s: No supports needed |]
printed |  | BOTTOM_COVER_V01 | 1 | --- | --- | --- | --- | [t: 19m |w: 1 |s: --- |]
printed |  | COVER_ROUND_V01 | 2 | --- | 1 | --- | --- | [t: 4m |w: 1 |s: No supports needed |]
printed |  | DISTANCE_LEFT_V01 | 1 | --- | --- | --- | --- | [t: 1h44m |w: 13 |s: No supports needed |]
printed |  | DISTANCE_RIGHT_V01 | 1 | --- | 1 | --- | --- | [t: 59m |w: 8 |s: No supports needed |]
printed |  | ENDCAP_BED-EXTRUSION_V01 | 2 | --- | --- | --- | --- | [t: 6m |w: 1 |s: No supports needed |]
printed |  | EXTRUDER_BASEPLATE_V01 | 1 | --- | 1 | --- | --- | [t: 7m |w: 1 |s: --- |]
printed |  | INTERCONNECT_V03_WIP | 1 | --- | --- | --- | --- | [t: --- |w: --- |s: --- |]
printed |  | LEADSCREW_NUT_MOUNT_V01 | 1 | --- | 1 | --- | --- | [t: 1h2m |w: 6 |s: No supports needed |]
printed |  | LED_INDICATOR_MOUNT_V01 | 1 | --- | 1 | --- | --- | [t: 16m |w: 1 |s: No supports needed |]
printed |  | MOTORBRACKET_LEFT_V01 | 1 | --- | 1 | --- | --- | [t: 3h17m |w: 32 |s: No supports needed |]
printed |  | MOTORBRACKET_RIGHT_V01 | 1 | --- | 1 | --- | --- | [t: 3h16m |w: 32 |s: No supports needed |]
printed |  | PICO_MOUNT_PRE-SKETCH_V01 | 1 | --- | 1 | --- | --- | [t: 20m |w: 2 |s: No supports needed |]
printed |  | SCREEN_BASE_V01_WIP | 1 | --- | --- | --- | --- | [t: 1h57m |w: 20 |s: Supports on build plate only |]
printed |  | SCREEN_LID_V01_WIP | 1 | --- | --- | --- | --- | [t: 1h6m |w: 9 |s: No supports needed |]
printed |  | SCREWMOUNT_BOTTOM_V01 | 1 | --- | 1 | --- | --- | [t: 59m |w: 7 |s: Supports on build plate only |]
printed |  | SIDE_PANEL_LEFT_V01 | 1 | --- | 1 | --- | --- | [t: 44m |w: 5 |s: No supports needed |]
printed |  | SIDE_PANEL_RIGHT_V01 | 1 | --- | 1 | --- | --- | [t: 44m |w: 5 |s: No supports needed |]
printed |  | X-RAIL_ENDCAP_V01 | 2 | --- | --- | --- | --- | [t: 6m |w: 1 |s: No supports needed |]
printed |  | XY-SPACER_V01 | 1 | --- | 1 | --- | --- | [t: 21m |w: 3 |s: No supports needed |]
printed |  | Z-AXIS-ENDSTOP_V01 | 1 | --- | 1 | --- | --- | [t: 1h2m |w: 8 |s: Supports on build plate only |]
printed |  | Z-BLOCK_HOLDER_V01 | 1 | --- | 1 | --- | --- | [t: 42m |w: 5 |s: No supports needed |]
category_info | Extruder |  |  | --- | --- | --- | ---
mechanical | Extruder | ANGLED_EXTRUDER_MOD | 1 | --- | --- | https://github.com/FramingApp/PositronV3B-High-Speed-Edition/blob/10x10makerbeams_w_screw_z_axis/CAD%20%20files/Angled%20Extruder%20Mod.stp | --- | Designed by HarryLoud: https://github.com/FramingApp/PositronV3B-High-Speed-Edition/blob/10x10makerbeams_w_screw_z_axis/CAD%20%20files/Angled%20Extruder%20Mod.stp
mechanical | Extruder | CAPRICORN_PTFE_TUBE_1 | 1 | 8,25€ | 1 | https://aliexpress.com/item/1005003433217588.html | https://amzn.to/3jBuaMN | About 60cm required
mechanical | Extruder | HOTEND_COMPLETE | 1 | 35,77€ | 1 | https://aliexpress.com/item/1005004802238357.html | --- | Funssor hotend complete / will be replaced with Phaetus hotend when available
category_info | electronics |  |  | --- | --- | --- | ---
mechanical | electronics | 10PIN_EXP_FEMALE | 1 | 0,88€ | 10 | https://aliexpress.com/item/1005002431897617.html | --- | Select 10P
mechanical | electronics | 10PIN_MALE_CONNECTOR | 1 | 1,12€ | 1 | https://aliexpress.com/item/33029492417.html | https://amzn.to/3XzUQMl | Select 2x5 10pin
mechanical | electronics | 6_PIN_MAGNETIC_POGO | 1 | 3,30€ | 1 | https://aliexpress.com/item/1005002669709542.html | --- | Select 6pin Straight
mechanical | electronics | C7_PLUG-IN | 1 | 0,23€ | 1 | https://aliexpress.com/item/4001252791878.html | ---
mechanical | electronics | CABLE_C7_SWITCH | 1 | 9,99€ | 1 | https://amzn.to/3w4nDgk | https://amzn.to/3XzU6qx | We recommend using a cable with a switch or an adapter like this: https://aliexpress.com/item/1005002301827800.html / https://amzn.to/3XzSGfH
mechanical | electronics | EPP-200-24 | 1 | 52,30€ | 1 | https://www.mouser.de/ProductDetail/MEAN-WELL/EPP-200-24?qs=C9r8PV%2F%252BoWOh4U0pNOxnkQ%3D%3D | https://amzn.to/3WfsBS9 | Meanwell EPP-200-24 !! Note from Muon3D: If theMuon3D heated bed is being used, the EPP-200-27 improves its performance by 30-40%. (70-80w at 24v, 90-100w at 27v). https://www.mouser.de/ProductDetail/MEAN-WELL/EPP-200-27?qs=C9r8PV%2F%252BoWPXQf6mJFm6HA%3D%3D
mechanical | electronics | FAN_2510 | 2 | 10,69€ | 2 | https://aliexpress.com/item/32807610078.html | https://amzn.to/3iCEaVR | 24V Dual Ball XH2,54
mechanical | electronics | FAN_3010 | 1 | 3,59€ | 1 | https://aliexpress.com/item/1005002568592831.html? | --- | Select 24V xh2.54 2pin
mechanical | electronics | FAN_5015 | 1 | 8,67€ | 1 | https://aliexpress.com/item/1005002517858129.html | https://aliexpress.com/item/32844339310.html | Select 24V model
mechanical | electronics | HEATED_GLASSBED_MUON-3D | 1 | 45,95€ | 1 | https://muon3d.com/products/positron-v3-transparent-heated-bed | --- | Highly recomended !! Note from Muon3D: If theMuon3D heated bed is being used, the EPP-200-27 improves its performance by 30-40%. (70-80w at 24v, 90-100w at 27v). https://www.mouser.de/ProductDetail/MEAN-WELL/EPP-200-27?qs=C9r8PV%2F%252BoWPXQf6mJFm6HA%3D%3D
mechanical | electronics | HEATER_CARTRIGE_1 | 1 | 1,27€ | 1 | https://aliexpress.com/item/32843289523.html | --- | Select 24V 50W 1M
mechanical | electronics | HEAT_SINK_RPI_2MM | 1 | 5,72€ | 1 | https://aliexpress.com/item/1005004772727034.html |  | 2mm height
mechanical | electronics | LED_4X_15X15 | 1 | 0,45€ | 1 | https://aliexpress.com/item/1005002674028098.html | --- | Select 4Bit Rectangular
mechanical | electronics | MINI_IR_SENSOR | 1 | 18,20€ | 1 | https://aliexpress.com/item/32995184975.html | ---
mechanical | electronics | MOTOR_17HS08-1004S | 3 | 8,28€ | 1 | https://www.omc-stepperonline.com/de/nema-17-bipolar-0-9deg-11ncm-15-6oz-in-1-2a-3-6v-42x42x21mm-4-draehte-17hm08-1204s | https://amzn.to/3iEKg85
mechanical | electronics | RPI_ZERO_2W | 1 | 22,50€ | 1 | https://www.reichelt.de/raspberry-pi-zero-2-w-4x-1-ghz-512-mb-ram-wlan-bt-rasp-pi-zero2-w-p313902.html | https://amzn.to/3IR9ASM | You can also use an Bananapi Pi M2 Zero as substituion: https://github.com/FramingApp/BananaPi_Positron_Klipper_Moonraker_Fluidd
mechanical | electronics | SKR-PICO | 1 | 29,99€ | 1 | https://biqu.equipment/en-au/products/btt-skr-pico-v1-0 | https://amzn.to/3QKw7Tj
mechanical | electronics | TFT_35 | 1 | 17,34€ | 1 | https://aliexpress.com/item/1005004864671870.html | https://amzn.to/3l8vAPt
mechanical | electronics | THERMISTOR_1 | 1 | 2,17€ | 5 | aliexpress.com/item/32812361274.html | https://amzn.to/3Y2qRxg | Select with XH2.54 terminal
category_info | fasteners |  |  | --- | --- | --- | ---
mechanical | fasteners | DIN_7979_M3X4X12 | 2 | 4,30€ | 5 | https://aliexpress.com/item/1005003200850626.html | --- | Select M3 (OD 4mm), 12mm (5pcs)
mechanical | fasteners | DIN_7991_M3X12 | 4 | 2,06€ | 50 | https://aliexpress.com/item/1005003107985358.html | https://amzn.to/3lbRscQ
mechanical | fasteners | DIN_7991_M3X14 | 41 | 2,28€ | 50 | https://aliexpress.com/item/1005003107985358.html | https://amzn.to/3JEOpDX
mechanical | fasteners | DIN_7991_M3X16 | 4 | 2,04 | 50 | https://aliexpress.com/item/1005003107985358.html | https://amzn.to/3l1bwhH
mechanical | fasteners | DIN_7991_M3X18 | 7 | 2,99€ | 50 | https://aliexpress.com/item/1005003107985358.html | ---
mechanical | fasteners | DIN_7991_M3X25 | 5 | 3,68€ | 50 | https://aliexpress.com/item/1005003107985358.html | https://amzn.to/3WZ3N0Z
mechanical | fasteners | DIN_7991_M3X35 | 12 | 4,72€ | 50 | https://aliexpress.com/item/1005003107985358.html | ---
mechanical | fasteners | DIN_7991_M3X8 | 8 | 1,58€ | 50 | https://aliexpress.com/item/1005003107985358.html | https://amzn.to/3wUBpmc
mechanical | fasteners | DIN_912_M3X20 | 5 | 1,48€ | 10 | https://aliexpress.com/item/1005003106092326.html | ---
mechanical | fasteners | DIN_912_M3X6 | 10 | 0,78€ | 10 | https://aliexpress.com/item/1005003106092326.html | ---
mechanical | fasteners | DIN_934_M3 | 2 | 1,36€ | 50 | https://aliexpress.com/item/1005003106199633.html | ---
mechanical | fasteners | M3_INSERT | 22 | 0,35€ | 50 | https://aliexpress.com/item/1005004879644825.html | https://amzn.to/3CRKrUf | Select M3(OD4.5mm), Length 5mm 50pcs
mechanical | fasteners | THUMBSCREW_M6X16 | 1 | 1,90€ | 2 | https://aliexpress.com/item/1005004651298319.html | --- | Select M6 2pcs, 16mm
mechanical | fasteners | WAFERHEAD_M3X10 | 19 | 1,97€ | 20 | https://aliexpress.com/item/1005004510664424.html | ---
mechanical | fasteners | WAFERHEAD_M3X14 | 4 | 2,10€ | 20 | https://aliexpress.com/item/1005004510664424.html | ---
mechanical | fasteners | WAFERHEAD_M3X20 | 5 | 2,54€ | 20 | https://aliexpress.com/item/1005004510664424.html | ---
category_info | makerbeam |  |  | 29,35€ | --- | --- | --- | Since Makerbeam does not sell beams with the needed length, they can either be cut by makerbeam or yourself. A cut by makerbeam costs 3.50€ you can find that service here: https://www.makerbeam.com/cut-and-tap-for-10x10mm.html . Either way, you need to buy beams that are able to be cut in the desired lengths for which we created a cutting plan that can be found here: https://github.com/Audiotronix/Positron_LT/blob/main/Parts/makerbeam_cuttingplan.pdf
mechanical | makerbeam | DIN_34805_M3X4 | 7 | --- | 25 | --- | --- | Included with T-slot nut
mechanical | makerbeam | DIN_7991_M3X4 | 3 | --- | 25 | --- | --- | Included with T-slot nut
mechanical | makerbeam | MAKERBEAM-CUBE | 3 | 17,95€ | 12 | https://www.makerbeam.com/makerbeam-corner-cubes-12p-black-for-makerbeam.html?id=24117589 | https://amzn.eu/2M0ya10 | You can buy single cubes here: https://amzn.eu/2M0ya10
mechanical | makerbeam | MAKERBEAM-CUBE_M6 | 1 | --- | --- | --- | --- | Included in previous cube order if ordered from makerbeam, otherwise can be ordered here: https://amzn.eu/2M0ya10
mechanical | makerbeam | MAKERBEAM_L-BRACKET_100304 | 7 | 6,95€ | 12 | https://www.makerbeam.com/makerbeam-90-degree-brackets-12p.html?id=24117637 | ---
mechanical | makerbeam | MAKERBEAM_L165 | 2 | -> | --- | https://www.makerbeam.com/makerbeam/makerbeam-10x10mm-profile-lengths-anodised-in-blac/ | --- | You can find more infos about the beams in the text below the category name https://github.com/Audiotronix/Positron_LT/tree/main/Parts#makerbeam
mechanical | makerbeam | MAKERBEAM_L200 | 2 | -> | --- | https://www.makerbeam.com/makerbeam/makerbeam-10x10mm-profile-lengths-anodised-in-blac/ | --- | You can find more infos about the beams in the text below the category name https://github.com/Audiotronix/Positron_LT/tree/main/Parts#makerbeam
mechanical | makerbeam | MAKERBEAM_L230 | 1 | -> | --- | https://www.makerbeam.com/makerbeam/makerbeam-10x10mm-profile-lengths-anodised-in-blac/ | --- | You can find more infos about the beams in the text below the category name https://github.com/Audiotronix/Positron_LT/tree/main/Parts#makerbeam
mechanical | makerbeam | MAKERBEAM_L240 | 2 | -> | --- | https://www.makerbeam.com/makerbeam/makerbeam-10x10mm-profile-lengths-anodised-in-blac/ | --- | You can find more infos about the beams in the text below the category name https://github.com/Audiotronix/Positron_LT/tree/main/Parts#makerbeam
mechanical | makerbeam | MAKERBEAM_L250 | 3 | -> | --- | https://www.makerbeam.com/makerbeam/makerbeam-10x10mm-profile-lengths-anodised-in-blac/ | --- | You can find more infos about the beams in the text below the category name https://github.com/Audiotronix/Positron_LT/tree/main/Parts#makerbeam
mechanical | makerbeam | MAKERBEAM_L30 | 1 | -> | --- | https://www.makerbeam.com/makerbeam/makerbeam-10x10mm-profile-lengths-anodised-in-blac/ | --- | You can find more infos about the beams in the text below the category name https://github.com/Audiotronix/Positron_LT/tree/main/Parts#makerbeam
mechanical | makerbeam | MAKERBEAM_T-NUT_101619-1 | 33 | 14,98€ | 25 | https://www.makerbeam.com/makerbeam-t-slot-nuts-for-makerbeam-25p.html | https://amzn.to/3DGxXPI | Order the big pack: https://www.makerbeam.com/makerbeam-t-slot-nuts-for-makerbeam-25p.html and a small one: https://www.makerbeam.com/linear-slide-kit-t-slot-nuts-5p-and-5mm-bolts-m3-1.html / https://amzn.to/3DGxXPI
category_info | motion |  |  | --- | --- | --- | ---
mechanical | motion | F5-10_BEARING | 2 | 0,27€ | 1 | https://aliexpress.com/item/4000211452548.html | https://amzn.to/3l24CZH
mechanical | motion | F683_OPEN_BEARING-H25- | 28 | 2,95€ | 10 | aliexpress.com/item/1005004282333265.html | --- | Select 3 times
mechanical | motion | GT2_16T_IDLER_SMOOTH | 1 | 0,55€ | 1 | https://aliexpress.com/item/32971394035.html | https://amzn.to/3DF3bad | Select 16T W6 B3 Without T
mechanical | motion | GT2_BELT-3MM_L1650MM | 1 | 5,00€ | 1 | https://www.ebay.de/itm/283457733982?var=585183190920 | https://amzn.to/3wUc9MT | Select x 2m (Y32) (You also can cut an 6mm belt in 2pieces. recommented cut at~2,8mm)
mechanical | motion | GT2_BELT-6MM_L178MM | 1 | 1,07€ | 1 | https://aliexpress.com/item/1005004100120790.html | https://amzn.to/3DIaihV | Select 2GT-178, Belt Width 6mm 1pcs
mechanical | motion | LEADSCREW_NUT_T5X4 | 1 | 1,49€ | 1 | https://www.ebay.de/itm/165688561910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 | --- | Only needs to be bought if no screw is included with rod! Select T5x1x4 Brass/POM
mechanical | motion | LEADSCREW_T5X4_L225 | 1 | 10,15€ | 1 | https://aliexpress.com/item/1005004583759873.html | https://www.ebay.de/itm/165688561901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 | Select 250mm, Pitch 1mm Lead 4mm / Second link has no screw!
mechanical | motion | MF85_BEARING | 2 | 0,72€ | 1 | https://aliexpress.com/item/1005004881583203.html | https://amzn.to/3HTb6mI | Select MF85ZZ 5X8X2.5mm
mechanical | motion | MGN12-C_CARRIAGE | 1 | --- | 1 | --- | --- | Mostly includet with the rails
mechanical | motion | MGN12_RAIL_L225 | 1 | 18,99€ | 1 | https://amzn.to/3H8WS0A | --- | 250mm MGN12C
mechanical | motion | MGN9-C_CARRIAGE | 1 | --- | 1 | --- | --- | Mostly includet with the rails
mechanical | motion | MGN9_RAIL_L227 | 1 | 20,99€ | 1 | https://amzn.to/3Wfy7UH | --- | 250mm MGN9C
mechanical | motion | MGW9-C_CARRIAGE | 1 | --- | 1 | --- | --- | Mostly includet with the rails
mechanical | motion | MGW9_RAIL_L227 | 1 | 19,40€ | 1 | https://www.ebay.de/itm/234306987115?var=533899872753 | https://amzn.to/3Xxt5Uz | 250mm MGW9C
mechanical | motion | MR115_BEARING | 1 | 0,94€ | 10 | https://aliexpress.com/item/32995122493.html | https://amzn.to/3HvHSsA
mechanical | motion | MR117_2Z_BEARING | 10 | 2,71€ | 5 | https://aliexpress.com/item/4000891798197.html | https://amzn.to/3RulK6u | Select MR117ZZ 7x11x3mm
mechanical | motion | PULLEY_T20_LOWPROFILE | 4 | 0,99€ | 1 | https://aliexpress.com/item/32913757229.html | --- | Select 20T Bore 5mm
category_info | shims |  |  | --- | --- | --- | ---
mechanical | shims | DIN_125_M5 | 2 | 1,48€ | 25 | https://aliexpress.com/item/1005002148389665.html | --- | Select M5(25PCS)
mechanical | shims | DIN_433_M3 | 12 | 2,21€ | 100 | https://aliexpress.com/item/4001213983709.html | --- | Select 3x6x0.5
mechanical | shims | DIN_988_7X13X02 | 40 | 1,91€ | 50 | https://aliexpress.com/item/1005002046188859.html | https://amzn.to/3DF8rdF | Select 50pcs M7x13xThick, Thick 0.2mm
mechanical | shims | DIN_988_M3X02 | 8 | 1,26€ | 50 | https://aliexpress.com/item/1005001878233881.html | https://amzn.to/3X3Y1LN | Select M3x6xThick 50pcs, 0.2mm thick
mechanical |  | BUFFER_BOTTOM | 4 | 1,06€ | 100 | https://aliexpress.com/item/1005001559607723.html | ---
mechanical |  | DUST_COVER_85X52 | 2 | --- | --- | https://aliexpress.com/item/4001283014835.html | --- | Highly recommended! need to be cutted in 85x52mm and clued under the air shrout left and right
mechanical |  | PCB_SCREEN_ADAPTER | 1 | --- | --- | --- | --- | Custom PCB, WIP
mechanical |  | SILICONE_SOCK_1 | 1 | --- | --- | --- | --- | Needs to be molded by yourself (WIP)
mechanical |  | SPACER_PRINTBED_WIP | 2 | --- | --- | --- | --- | Bed-End-Spacer WIP

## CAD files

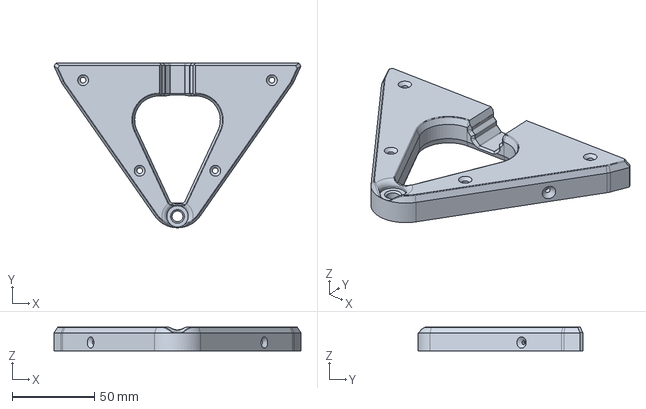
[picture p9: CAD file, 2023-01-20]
Parts/Printed Parts/STEP/BED_HOLDER_MAIN_V01.step
150.3 x 100.2 x 14.5 mm

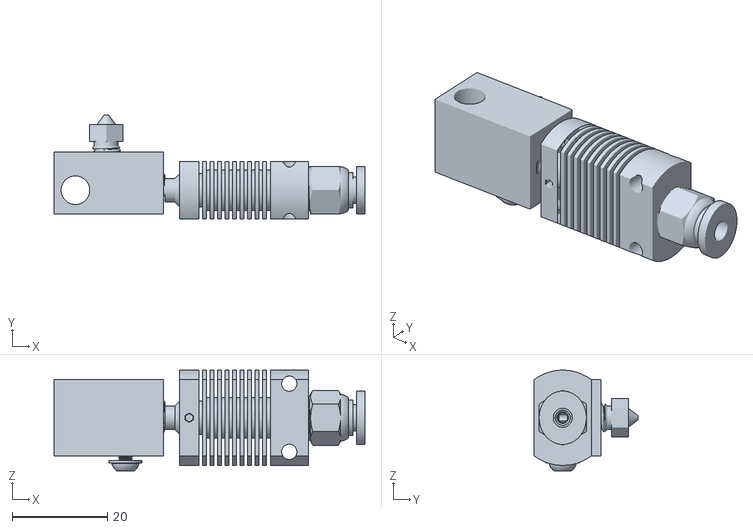
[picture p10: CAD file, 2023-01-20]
Parts/Mechanical Parts/HOTEND_COMPLETE.stl
65.3 x 21.8 x 21.1

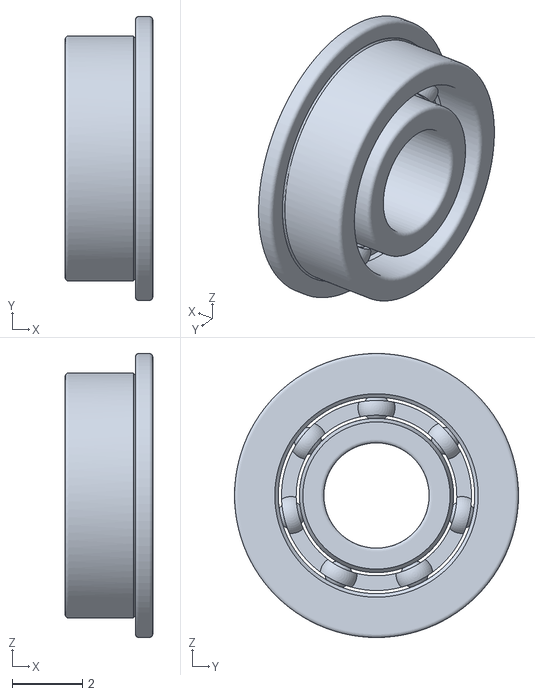
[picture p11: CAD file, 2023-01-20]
Parts/Mechanical Parts/F683_OPEN_BEARING-H25-.stl
2.50 x 8.10 x 8.10

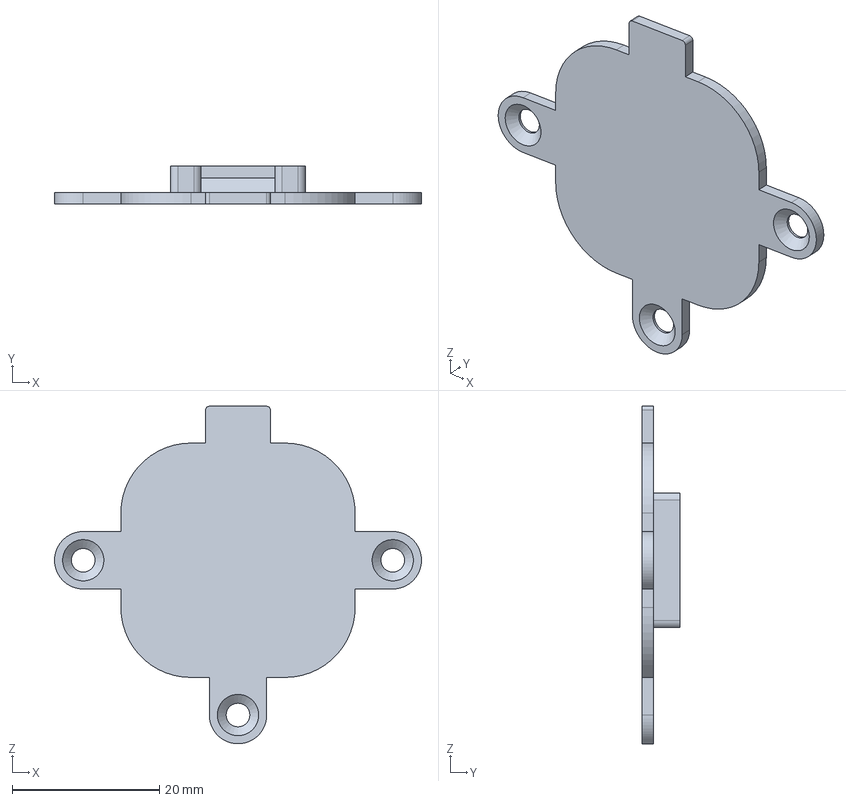
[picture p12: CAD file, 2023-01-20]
Parts/Printed Parts/STEP/LED_INDICATOR_MOUNT_V01.step
49.8 x 5.10 x 45.8 mm

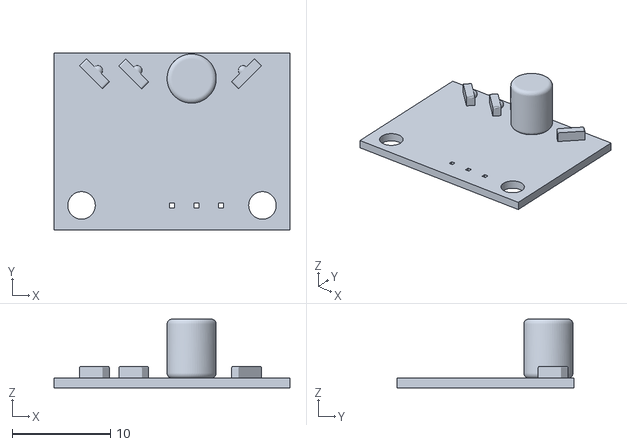
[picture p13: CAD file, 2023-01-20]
Parts/Mechanical Parts/MINI_IR_SENSOR.stl
24.0 x 18.0 x 7.00

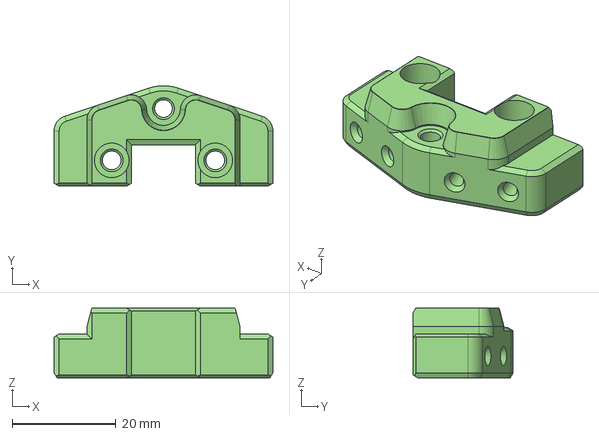
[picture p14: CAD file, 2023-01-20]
Parts/Printed Parts/STEP/BELT_TENSIONER_XY_V01.step
42.3 x 19.4 x 13.5 mm

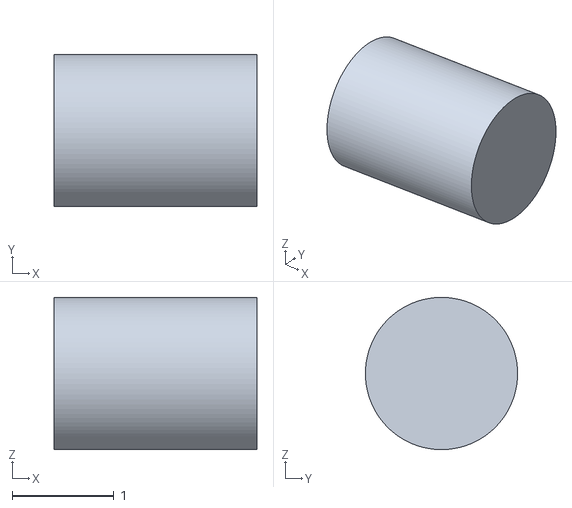
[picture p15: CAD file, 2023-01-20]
Parts/Mechanical Parts/THERMISTOR_1.stl
2.00 x 1.50 x 1.50

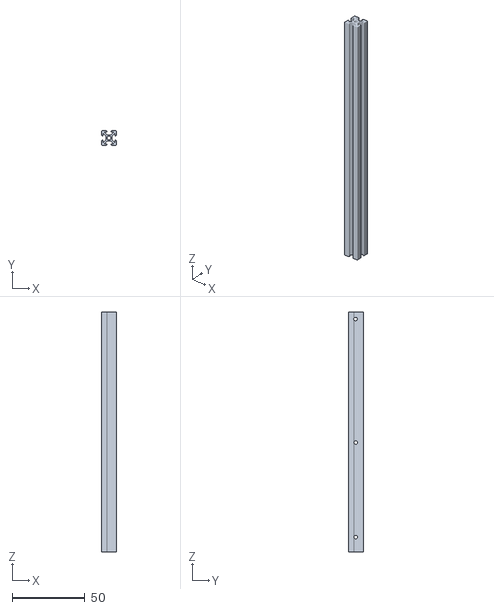
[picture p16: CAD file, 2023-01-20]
Parts/Mechanical Parts/MAKERBEAM_L165.stl
10.0 x 10.0 x 165.0

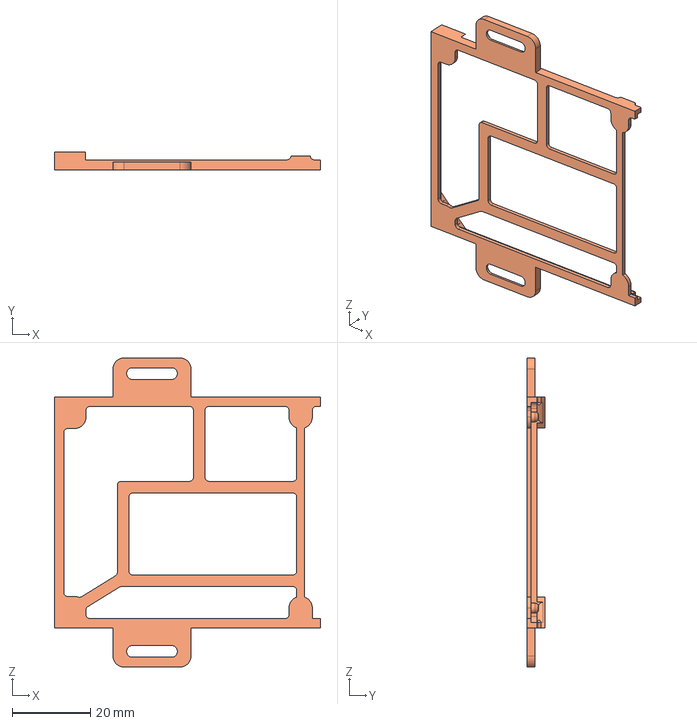
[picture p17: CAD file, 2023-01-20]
Parts/Printed Parts/STEP/PICO_MOUNT_PRE-SKETCH_V01.step
68.2 x 4.60 x 79.2 mm

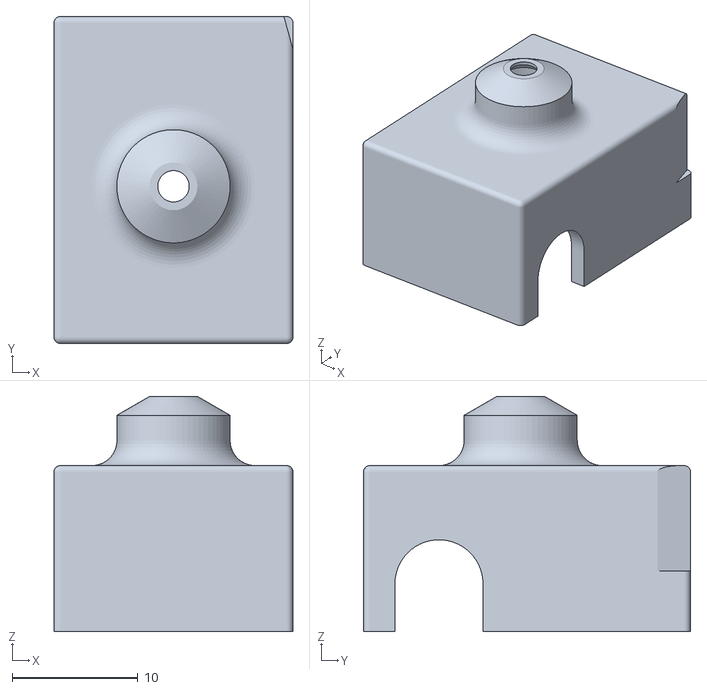
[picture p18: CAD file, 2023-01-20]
Parts/Mechanical Parts/SILICONE_SOCK_1.stl
19.0 x 26.0 x 18.7

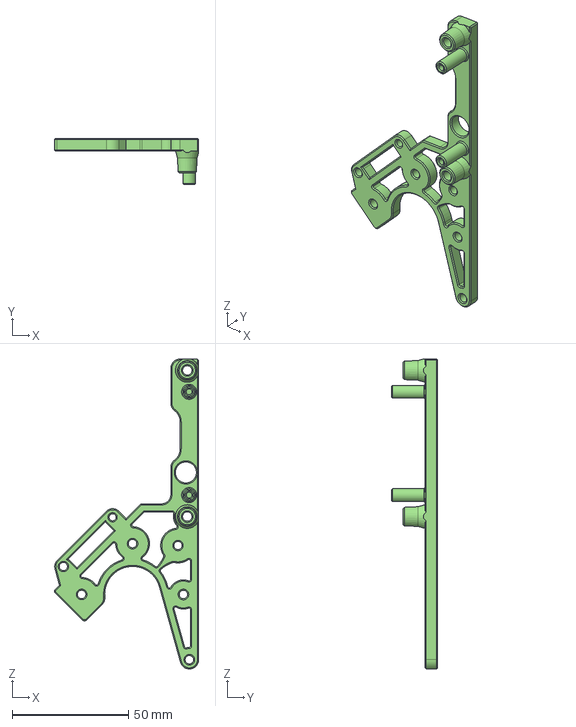
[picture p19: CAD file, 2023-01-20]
Parts/Printed Parts/STEP/DISTANCE_LEFT_V01.step
62.2 x 20.0 x 133.6 mm

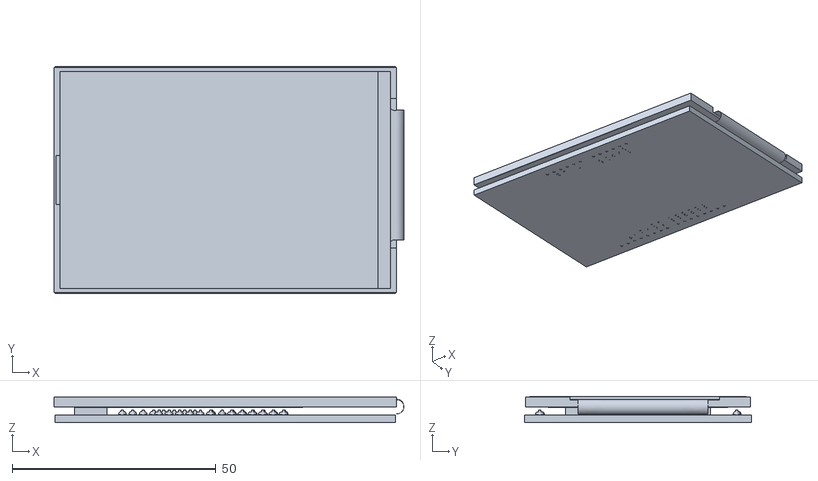
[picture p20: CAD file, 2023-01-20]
Parts/Mechanical Parts/TFT_35.stl
85.8 x 55.6 x 6.44

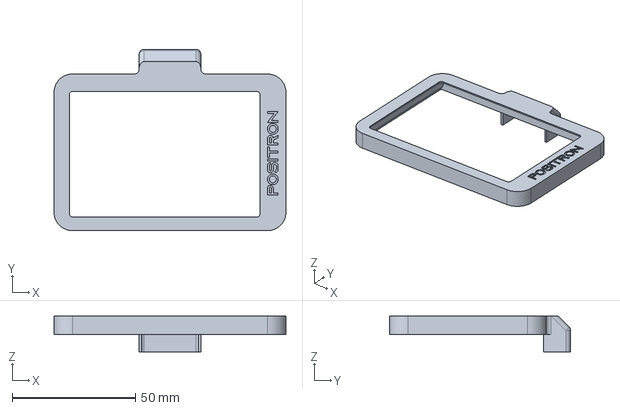
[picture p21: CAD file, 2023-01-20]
Parts/Printed Parts/STEP/SCREEN_LID_V01_WIP.step
94.0 x 73.5 x 14.4 mm

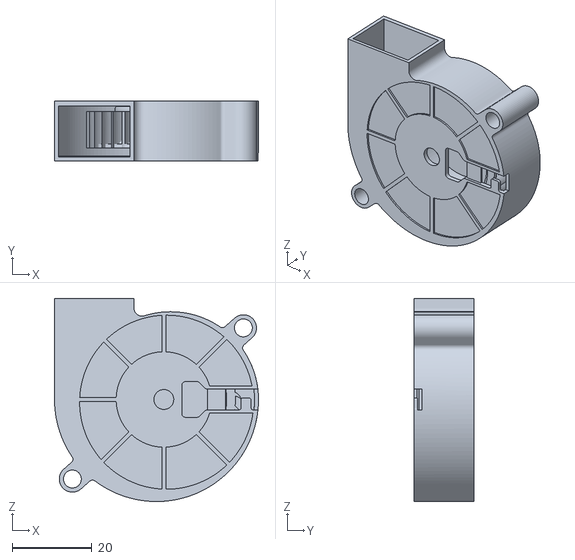
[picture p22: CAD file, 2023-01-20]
Parts/Mechanical Parts/FAN_5015.stl
51.3 x 15.0 x 51.1

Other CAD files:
Parts/Printed Parts/STEP/MOTORBRACKET_RIGHT_V01.step
Parts/Mechanical Parts/SKR-PICO.stl
Parts/Printed Parts/STEP/COVER_ROUND_V01.step
Parts/Printed Parts/STEP/BELT-TENSIONER_Z_V01.step
Parts/Mechanical Parts/10PIN_EXP_FEMALE.stl
Parts/Mechanical Parts/10PIN_MALE_CONNECTOR.stl
Parts/Mechanical Parts/6_PIN_MAGNETIC_POGO.stl
Parts/Mechanical Parts/BUFFER_BOTTOM.stl
Parts/Mechanical Parts/C7_PLUG-IN.stl
Parts/Mechanical Parts/CABLE_C7_SWITCH.stl
Parts/Mechanical Parts/CAPRICORN_PTFE_TUBE_1.stl
Parts/Mechanical Parts/DIN_125_M5.stl
Parts/Mechanical Parts/DIN_34805_M3X4.stl
Parts/Mechanical Parts/DIN_433_M3.stl
Parts/Mechanical Parts/DIN_7979_M3X4X12.stl
Parts/Mechanical Parts/DIN_7991_M3X12.stl
Parts/Mechanical Parts/DIN_7991_M3X14.stl
Parts/Mechanical Parts/DIN_7991_M3X16.stl
Parts/Mechanical Parts/DIN_7991_M3X18.stl
Parts/Mechanical Parts/DIN_7991_M3X25.stl
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

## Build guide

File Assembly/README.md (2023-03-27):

# Assembling the Positron LT

## Required tools:
- Saw (aluminium & Steel)
- Drill (aluminium)
- Screwdriver
- Soldering iron

## Optional tools:
- Tap

<br>

# Preparation:

### Cutting everything to length:

#### Makerbeams
You can find a cutting plan [here](https://github.com/Fliens/Positron_LT/blob/main/Parts/makerbeam_cuttingplan.pdf)

Required lengths:
- 165mm x2
- 200mm x2
- 230mm x1
- 240mm x2
- 250mm x3
- 30mm x1

#### Linear rails:
MGN9_RAIL (250mm): 227mm
MGW9_RAIL (250mm): 227mm
MGN12_RAIL (250mm): 235mm

### Inserting inserts into the printed parts:

> Images comming soon

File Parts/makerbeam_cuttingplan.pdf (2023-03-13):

Linear Cutting Plan / optiCutter

Layout patterns

Created by www.opticutter.com

Required stocks

Stock length | Quantity

900 2

600 1

Total | 3
Kerf / Blade thickness | 10
Total parts | 11
Total parts length | 2,220
Used stocks total length | 2,400
Total yield | 92.5 %
Repetition | Layout ID | Stock length | Cuts | Material remnant | Cut waste
2x | A | 900 | [ 1x 250 ] [ 1x 240 ] [ 1x 200 ] [ 1x 165 ] | 5 | 40
1x | B | 600 | [ 1x 250 ] [ 1x 230 ] [ 1x 30 ] | 60 | 30

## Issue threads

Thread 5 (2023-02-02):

Add EPP-200-27 as an option to the BOM

FramingApp, 2023-02-02:
If the https://muon3d.com/products/positron-v3-transparent-heated-bed is being used, the EPP-200-27 improves its performance by 30-40%. (70-80w at 24v, 90-100w at 27v).
Also, recommend to turn the voltage via the potentiometer up to the max to further increase the voltage and increase heated bed performance.

Closed 2023-02-03.

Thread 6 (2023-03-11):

Why is the hotend limited to 250C?

kozross, 2023-03-11:
Is it PTFE-lined or something? If so, that's quite disappointing, as it severely limits what materials can be printed.

Audiotronix, 2023-03-11:
Because its just a Mod of KRALYNS  Positron V3 which is limited to 250, like u know
But yeah, u are completly right, u are also limited by Bed Temperatur for Materials.
The Phaetus Hotend, we are all waiting for, is not released yet.

And everything is still work in progress :-)

Closed 2023-03-11.

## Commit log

2023-01-05 Init step for printed parts
2023-01-05 Created CAD dir
2023-01-07 Added bom
    [bom.csv]
2023-01-07 Added 3d files for each part
    [100304.step, 100304.stl, 101619-1.step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]
2023-01-07 Added amount to printed parts
2023-01-07 Adjusted csv
    [bom.csv]
2023-01-07 Changed parts readme
    [100304.step, 100304.stl, 101619-1.step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]
2023-01-08 Reset bom
    [bom.csv]
2023-01-08 Removed _AF
    [bom.csv]
2023-01-08 New BOM
    [bom.csv]
2023-01-08 Removed _PR
    [bom.csv]
2023-01-08 Added some categories
    [bom.csv]
2023-01-08 Added auto bom formatting
2023-01-08 Auto updated readme table
    [bom.csv]
2023-01-09 Added cutting plan
    [bom.csv]
2023-01-09 BOM fix
    [bom.csv]
2023-01-09 Added categories
    [bom.csv]
2023-01-10 Removed test
    [bom.csv]
2023-01-14 Added category_info
    [bom.csv]
2023-01-14 Added makerbeam note
    [bom.csv]
2023-01-14 Added info
    [bom.csv]
2023-01-14 Added pcs
    [bom.csv]
2023-01-14 Added cats
    [bom.csv]
2023-01-15 Added links
    [bom.csv]
2023-01-15 Added prices
    [bom.csv]
2023-01-15 More notes
    [bom.csv]
2023-01-15 Added link
    [bom.csv]
2023-01-16 Added motor info
    [bom.csv]
2023-01-16 Added missing products
    [bom.csv]
2023-01-16 Fixed names
    [bom.csv]
2023-01-16 Missing 3d files
    [BASECOVER_LEFT_V01.step, BASECOVER_RIGHT_V01.step, BASECOVER_RIGHT_V01.stl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]
2023-01-18 Added action filter
2023-01-19 Relative cutting plan links
    [bom.csv]
2023-01-19 Add files via upload
    Printing orientation
2023-01-20 Added folders to gallery
    [bom.csv]
2023-01-20 Added printed info action
2023-01-20 Auto format
    [bom.csv]
2023-01-20 More Info
    [bom.csv]
2023-01-20 Print info
    [bom.csv]
2023-01-21 Added more makerbeam links.. price gets cheaper
    [bom.csv]
2023-03-13 Updated makerbeam recommendation for cheaper shipping costs
    [bom.csv, optiCutter-config.csv]
2023-03-13 Added message for makerbeams
    [bom.csv]
2023-04-26 Update bom.csv (#8)
    [bom.csv]
2023-05-19 Revert "Update bom.csv (#8)"
    This reverts commit 29488a9b7629eaab1f596520bfb39668f587a702.
    [bom.csv]
2023-09-18 Bom update (#12)
    * Update bom.csv
    * Auto format
    * Update README.md
    * Update bom.csv
    * Auto format
    * Update README.md
    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
    [bom.csv]
